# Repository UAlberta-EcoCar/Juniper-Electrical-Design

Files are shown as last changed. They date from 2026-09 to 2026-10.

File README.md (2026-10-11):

# Juniper-Electrical-Design - FOC Board

The FOC Board is planned to be on the car's steering wheel.
This branch currently contains the schematic and PCB files for the board.
For firmware see [https://github.com/UAlberta-EcoCar/Sally-Dashboard](https://github.com/UAlberta-EcoCar/Sally-Dashboard)

Board Requirements:
* A LCD screen with touch screen capabilities
* An IMU to track steering wheel position
* &gt; 3 Inputs for push buttons
* CAN FD capability 
* Addressable RGB LEDs
* Powered by a 7V and 12V power supply
* Overcurrent protection

MCU Chosen: STM32G491RET6

Link: https://www.digikey.ca/en/products/detail/stmicroelectronics/STM32G491RET6/13592591
* The STM32F4 series was considered, 
 but an MCU with the right stock options, clock speed, protocol support, and pin count was not found.

# Getting Started

Clone the repository:

```sh
git clone --recursive https://github.com/UAlberta-EcoCar/Juniper-Electrical-Design.git
```

Switch to the branch:

```sh
git checkout FOC-Board
```

Onboarding documentation here: [https://ualberta-ecocar.github.io/Documentation/](https://ualberta-ecocar.github.io/Documentation/)

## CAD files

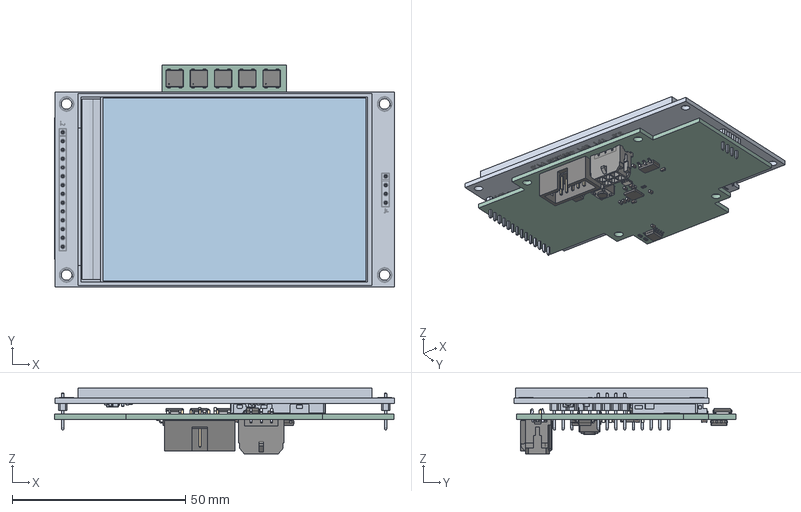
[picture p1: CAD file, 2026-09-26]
FOC_PCB/foc_driver_board.step
98.2 x 64.1 x 19.0 mm
C_0603_1608Metric x 19
3.5 TFT Module - No Glass
glass
SOIC_8_39x49mm_P127mm x 2
R_0603_1608Metric x 4
Crystal_SMD_3225-4Pin_3.2x2.5mm
SOT_223 x 2
QFN-32-1EP_5x5mm_Pitch0.5mm
IDC_Header_2x05_P254mm_Vertical
L_0603_1608Metric
SW_PUSH_6mm
foc_driver_board_PCB

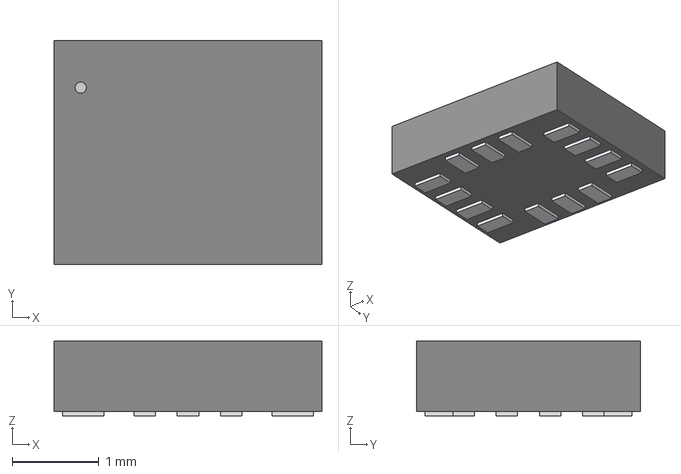
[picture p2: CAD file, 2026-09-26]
FOC_PCB/PartsLibrary/LSM6DSO32/LGA-14L_2P5X3X0P83_STM.step
3.10 x 2.59 x 0.866 mm

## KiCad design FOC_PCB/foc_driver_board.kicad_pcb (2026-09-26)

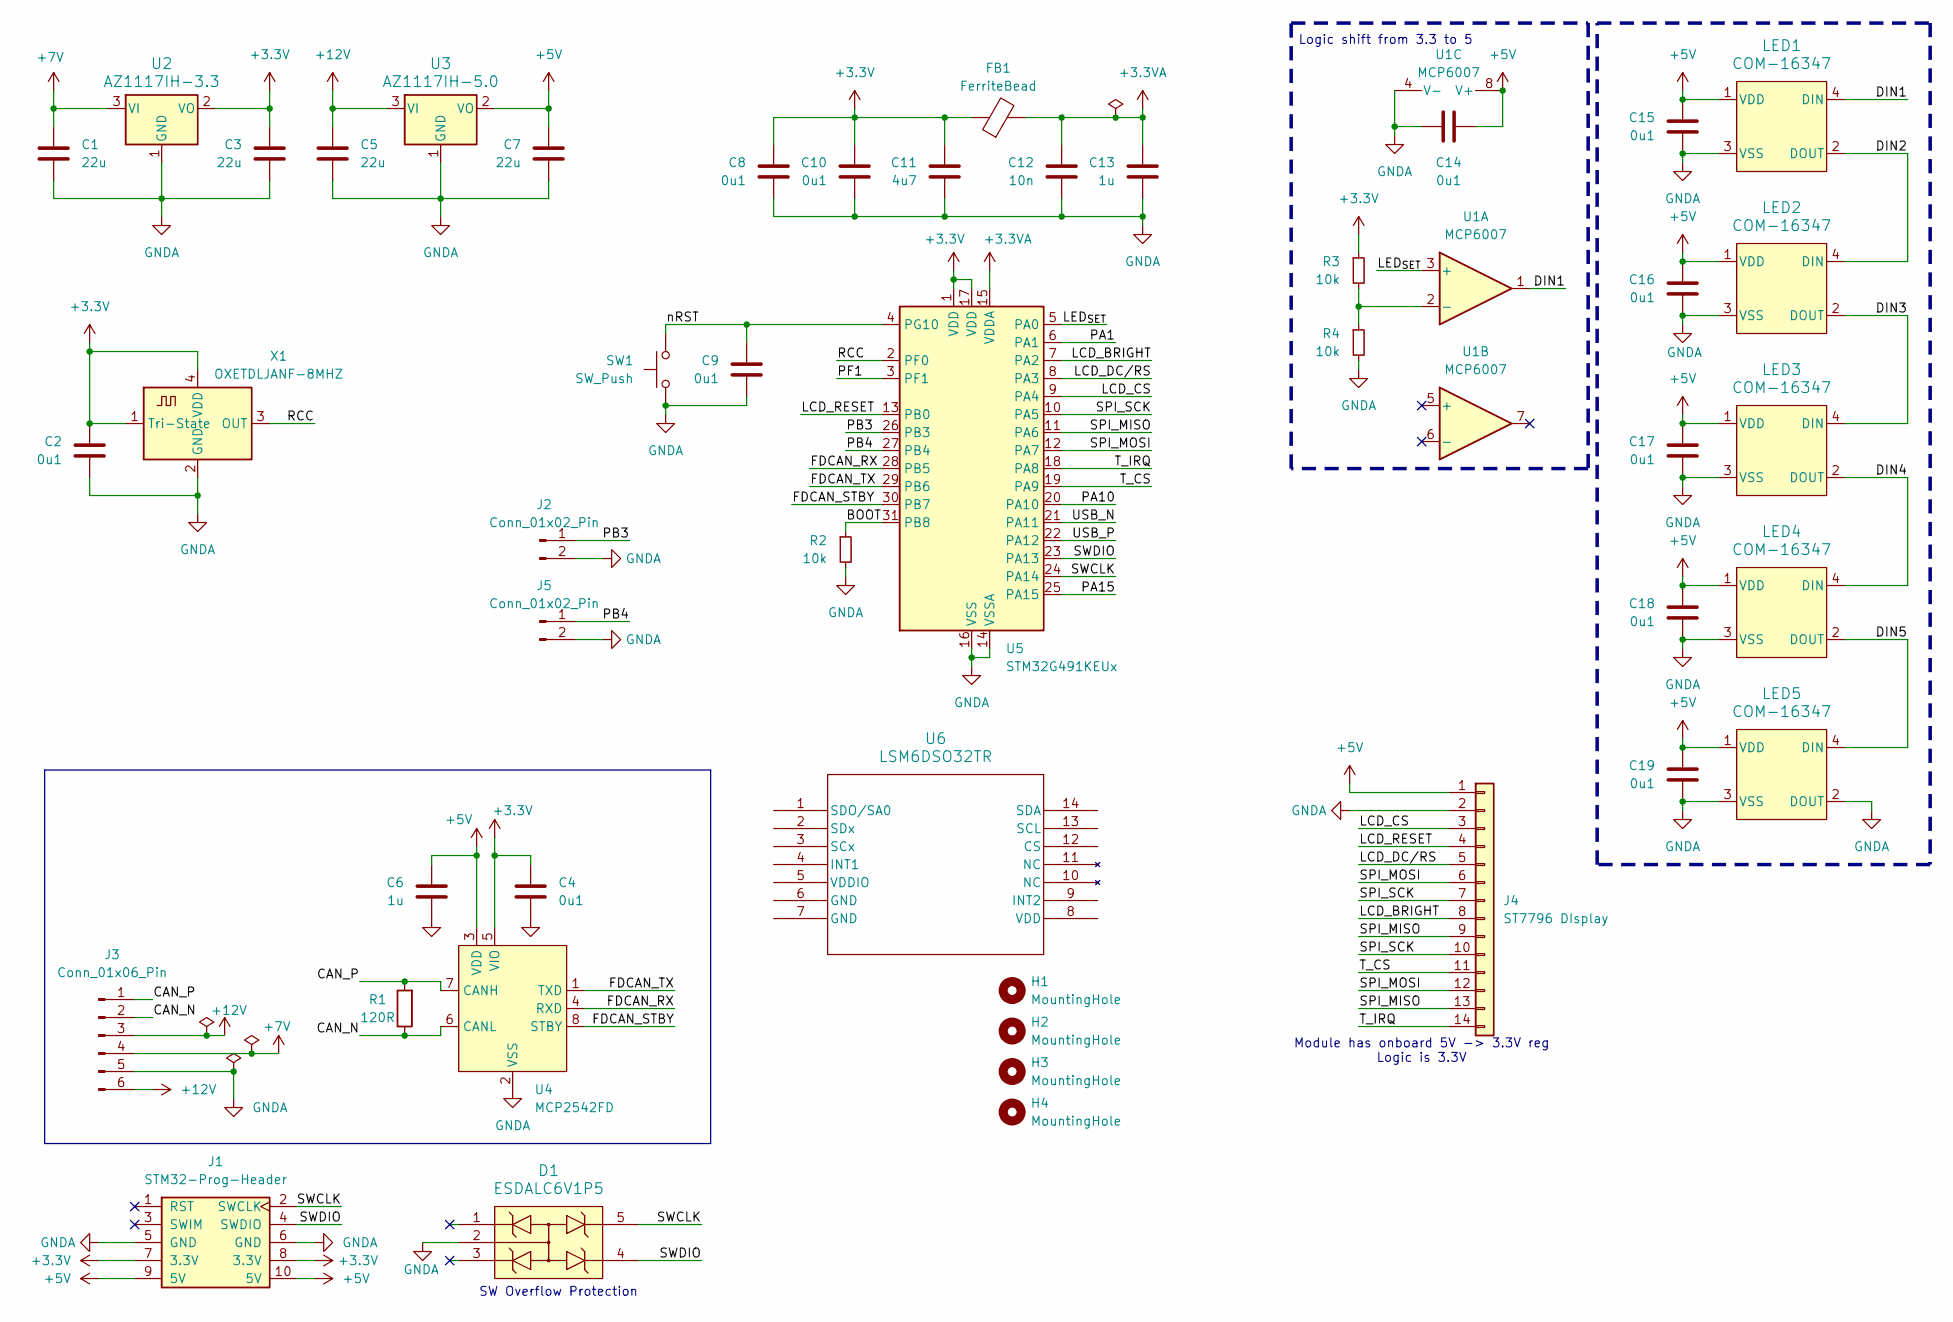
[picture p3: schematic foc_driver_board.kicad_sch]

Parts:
C1, C3, C5, C7: 22u; C_0603_1608Metric
C2, C4, C8, C9, C10, C14, C15, C16, C17, C18, C19: 0u1; C_0603_1608Metric
C6, C13: 1u; C_0603_1608Metric
C11: 4u7; C_0603_1608Metric
C12: 10n; C_0603_1608Metric
D1: ESDALC6V1P5
FB1: FerriteBead; L_0603_1608Metric
H1, H2, H3, H4: MountingHole; MountingHole_3.2mm_M3
J1: STM32-Prog-Header; IDC-STM32-Prog-Header_2x05_P2.54mm_Vertical
J2, J5: Conn_01x02_Pin; PinSocket_1x02_P2.54mm_Vertical
J3: Conn_01x06_Pin; STD_PWR_HEADER
J4: ST7796 DIsplay; ILI9488
LED1, LED2, LED3, LED4, LED5: COM-16347; COM-16347_SPK
R1: 120R; R_0603_1608Metric
R2, R3, R4: 10k; R_0603_1608Metric
SW1: SW_Push; SW_PUSH_6mm
U1: MCP6007; SOIC-8_3.9x4.9mm_P1.27mm
U2: AZ1117IH-3.3; SOT-223-3_TabPin2
U3: AZ1117IH-5.0; SOT-223-3_TabPin2
U4: MCP2542FD; SOIC-8_3.9x4.9mm_P1.27mm
U5: STM32G491KEUx; QFN-32-1EP_5x5mm_P0.5mm_EP3.45x3.45mm
U6: LSM6DSO32TR; LGA-14L_2P5X3X0P83_STM
X1: OXETDLJANF-8MHZ; Crystal_SMD_3225-4Pin_3.2x2.5mm

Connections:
+3.3V: C2.1, C3.1, C4.1, C8.1, C10.1, C11.1, FB1.1, J1.7 (3.3V), J1.8 (3.3V), R3.1, U2.2 (VO), U4.5 (VIO), U5.1 (VDD), U5.17 (VDD), X1.1 (Tri-State), X1.4 (VDD)
+3.3VA: C12.1, C13.1, FB1.2, U5.15 (VDDA)
+5V: C6.1, C7.1, C14.1, C15.1, C16.1, C17.1, C18.1, C19.1, J1.9 (5V), J1.10 (5V), J4.1, LED1.1 (VDD), LED2.1 (VDD), LED3.1 (VDD), LED4.1 (VDD), LED5.1 (VDD), U1.8 (V+), U3.2 (VO), U4.3 (VDD), U6.8 (V+)
+12V: C5.1, J3.3, J3.6, U3.3 (VI)
/BOOT: R2.1, U5.31 (PB8)
/CAN_N: J3.2, R1.1, U4.6 (CANL)
/CAN_P: J3.1, R1.2, U4.7 (CANH)
/DIN1: LED1.4 (DIN), U1.1, U6.1 (SDO/SA0)
/DIN2: LED1.2 (DOUT), LED2.4 (DIN)
/DIN3: LED2.2 (DOUT), LED3.4 (DIN)
/DIN4: LED3.2 (DOUT), LED4.4 (DIN)
/DIN5: LED4.2 (DOUT), LED5.4 (DIN)
/FDCAN_RX: U4.4 (RXD), U5.28 (PB5)
/FDCAN_STBY: U4.8 (STBY), U5.30 (PB7)
/FDCAN_TX: U4.1 (TXD), U5.29 (PB6)
/LCD_BRIGHT: J4.8, U5.7 (PA2)
/LCD_CS: J4.3, U5.9 (PA4)
/LCD_DC/RS: J4.5, U5.8 (PA3)
/LCD_RESET: J4.4, U5.13 (PB0)
/LED_{SET}: U1.3 (+), U5.5 (PA0), U6.3 (+)
/PA1: U5.6 (PA1)
/PA10: U5.20 (PA10)
/PA15: U5.25 (PA15)
/PB3: J2.1, U5.26 (PB3)
/PB4: J5.1, U5.27 (PB4)
/PF1: U5.3 (PF1)
/RCC: U5.2 (PF0), X1.3 (OUT)
/SPI_MISO: J4.9, J4.13, U5.11 (PA6)
/SPI_MOSI: J4.6, J4.12, U5.12 (PA7)
/SPI_SCK: J4.7, J4.10, U5.10 (PA5)
/SWCLK: D1.5, J1.2 (SWCLK), U5.24 (PA14)
/SWDIO: D1.4, J1.4 (SWDIO), U5.23 (PA13)
/T_CS: J4.11, U5.19 (PA9)
/T_IRQ: J4.14, U5.18 (PA8)
/USB_N: U5.21 (PA11)
/USB_P: U5.22 (PA12)
/nRST: C9.1, SW1.2, U5.4 (PG10)
GNDA: C1.2, C2.2, C3.2, C4.2, C5.2, C6.2, C7.2, C8.2, C9.2, C10.2, C11.2, C12.2, C13.2, C14.2, C15.2, C16.2, C17.2, C18.2, C19.2, D1.2, J1.5 (GND), J1.6 (GND), J2.2, J3.5, J4.2, J5.2, LED1.3 (VSS), LED2.3 (VSS), LED3.3 (VSS), LED4.3 (VSS), LED5.2 (DOUT), LED5.3 (VSS), R2.2, R4.2, SW1.1, U1.4 (V-), U2.1 (GND), U3.1 (GND), U4.2 (VSS), U5.14 (VSSA), U5.16 (VSS), U5.32 (VSS), U5.33 (VSS), U6.4 (V-), X1.2 (GND)
VCC: C1.1, J3.4, U2.3 (VI)

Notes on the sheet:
SW Overflow Protection
Logic shift from 3.3 to 5
Module has onboard 5V -> 3.3V reg Logic is 3.3V

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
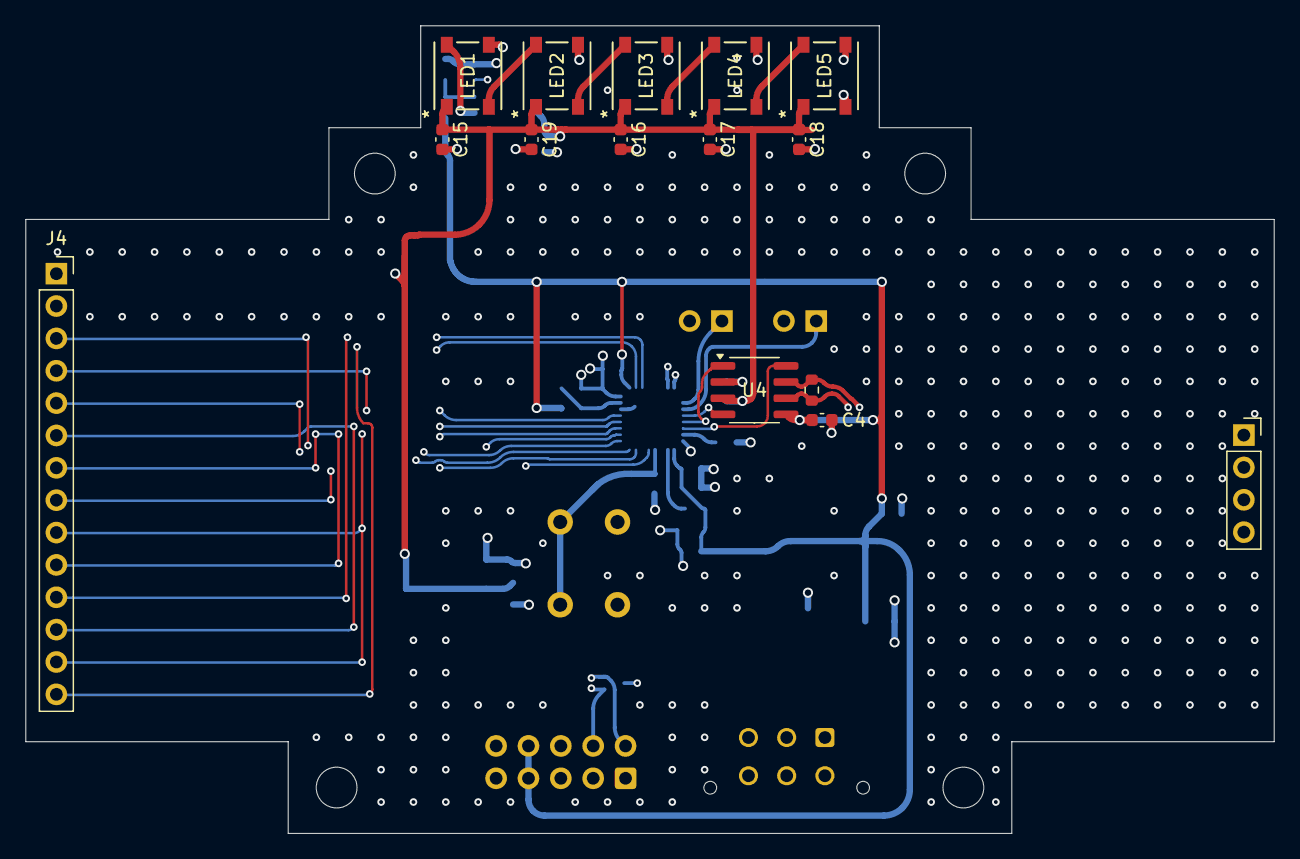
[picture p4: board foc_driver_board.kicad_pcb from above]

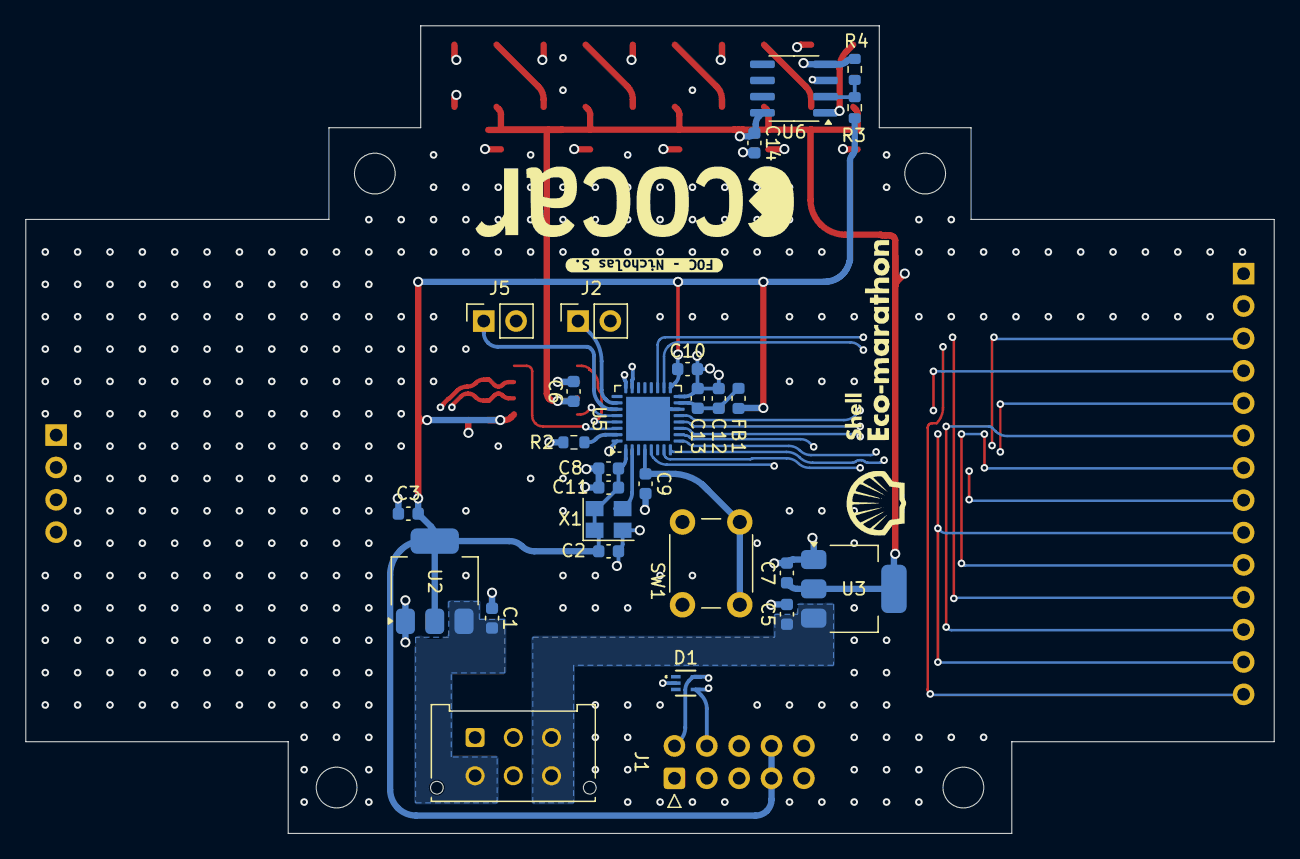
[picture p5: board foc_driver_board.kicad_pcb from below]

Board: 4 copper layers, 98.0 x 63.4 mm, 47 parts (29 on the bottom side), 34 nets.

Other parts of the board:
kibuzzard-678986CF: G***; kibuzzard-678986CF

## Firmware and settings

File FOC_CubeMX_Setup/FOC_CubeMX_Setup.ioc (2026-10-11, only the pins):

Mcu.UserName=STM32G491RETx
PA1.GPIO_Label=T_IRQ
PA1.Signal=GPXTI1
PA10.GPIO_Label=FDCAN_STBY
PA10.Signal=GPIO_Output
PA11.Signal=FDCAN1_RX
PA12.Signal=FDCAN1_TX
PA13.Signal=SYS_JTMS-SWDIO
PA14.Signal=SYS_JTCK-SWCLK
PA15.GPIO_Label=IMU_SCL
PA15.Signal=I2C1_SCL
PA3.GPIO_Label=T_CS
PA3.Signal=GPIO_Output
PA4.GPIO_Label=LCD_BRIGHT
PA4.Signal=GPIO_Output
PA5.Signal=SPI1_SCK
PA6.Signal=SPI1_MISO
PA7.Signal=SPI1_MOSI
PB0.GPIO_Label=LCD_CS
PB0.Signal=GPIO_Output
PB14.GPIO_Label=BTN1
PB14.Signal=GPXTI14
PB15.GPIO_Label=BTN2
PB15.Signal=GPXTI15
PB3.Signal=SYS_JTDO-SWO
PB7.GPIO_Label=IMU_SDA
PB7.Signal=I2C1_SDA
PC10.GPIO_Label=IMU_CS
PC10.Signal=GPIO_Output
PC11.GPIO_Label=IMU_SA0
PC11.Signal=GPIO_Output
PC12.GPIO_Label=IMU_INT1
PC12.Signal=GPXTI12
PC4.GPIO_Label=LCD_DC
PC4.Signal=GPIO_Output
PC5.GPIO_Label=LCD_RESET
PC5.Signal=GPIO_Output
PC6.GPIO_Label=LED_IN
PC6.Signal=S_TIM8_CH1
PD2.GPIO_Label=IMU_INT2
PD2.Signal=GPXTI2
PF0-OSC_IN.Signal=RCC_OSC_IN
